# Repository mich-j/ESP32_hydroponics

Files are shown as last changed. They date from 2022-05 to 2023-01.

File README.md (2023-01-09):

# ESP32_hydroponics: IoT hydroponics setup with telemetry

System designed for easy crop cultivation at home, especially herbs and fast-growing small plants like lettuce. Three channels, with continous flow of a nutrient solution, are available, allowing for up to 12 seedlings to be grown at the same time.

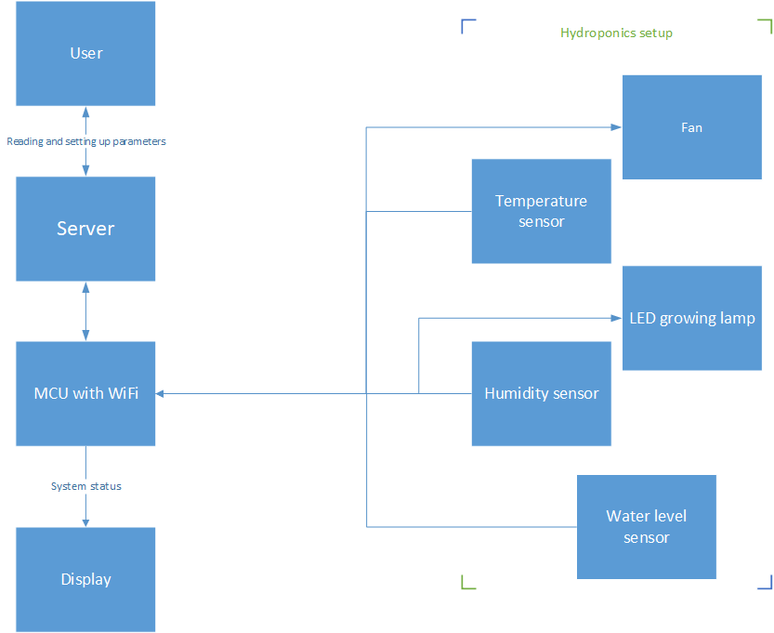
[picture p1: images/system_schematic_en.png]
schematic


ESP32 Devkit module was used to process data from sensors and publish messages with telemetry via MQTT.

Code was written using Arduino Framework for ESP32, in Visual Studio Code with Platformio extension.

### Features
- Air temperature and humidity measurement
- Built as a Nutrient Film Technique (NFT) system
- Remote control via MQTT protocol
- Dashboard with gauges and charts
- PWM LED control
- Low water level alert
- Fan for controlling humidity and supplying oxygen
- OLED screen for easy operation control

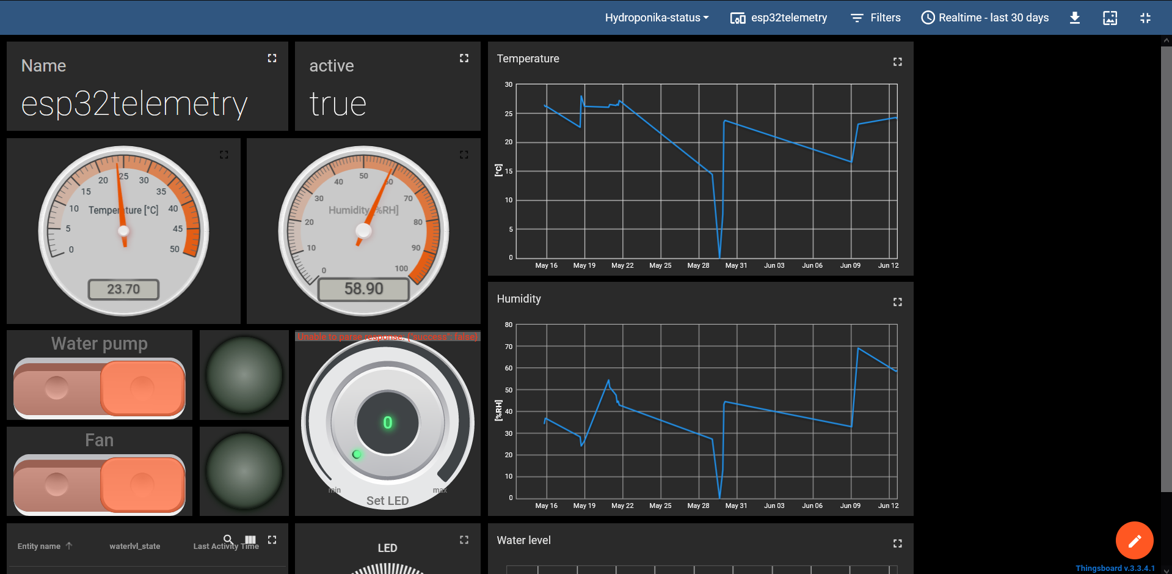
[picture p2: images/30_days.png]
administrator's dashboard

_Dashboard for system's administrator_
  
 ### Communication 

Raspberry Pi 3B+ hosts Thingsboard server, which allows to store sensors' output in a database and display a dashboard with charts and gauges, accessible within local network. User can turn on/off water pump and fan. Moreover, LED intensity can be controlled with a dimmer. Raspberry also works as a MQTT broker and a gateway for communication with Thingsboard.

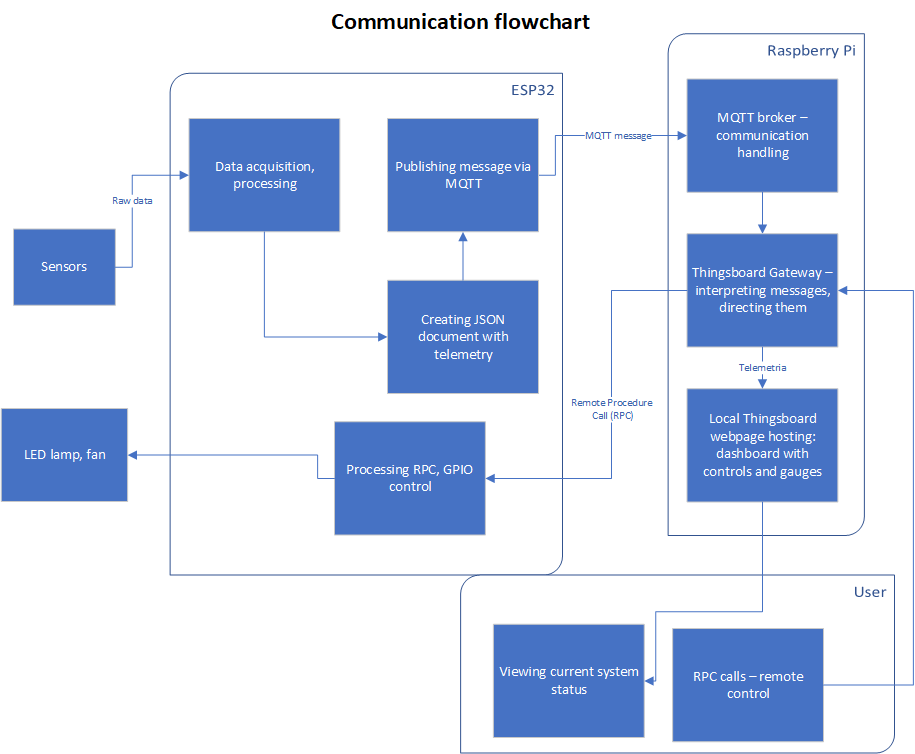
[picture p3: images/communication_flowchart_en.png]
communication schema
 

### Used software:
- [Mosquitto MQTT broker](https://mosquitto.org/)
- [Thingsboard Community server](https://thingsboard.io/)

### Used libraries:
- [SimpleDHT](https://github.com/winlinvip/SimpleDHT) 
- [u8g2](https://github.com/olikraus/u8g2)
- [ESP32 Timer Interrupt](https://github.com/khoih-prog/ESP32TimerInterrupt)
- [PubSub Client](https://github.com/knolleary/pubsubclient)
- [ArduinoJson](https://github.com/bblanchon/ArduinoJson)

### Built prototype

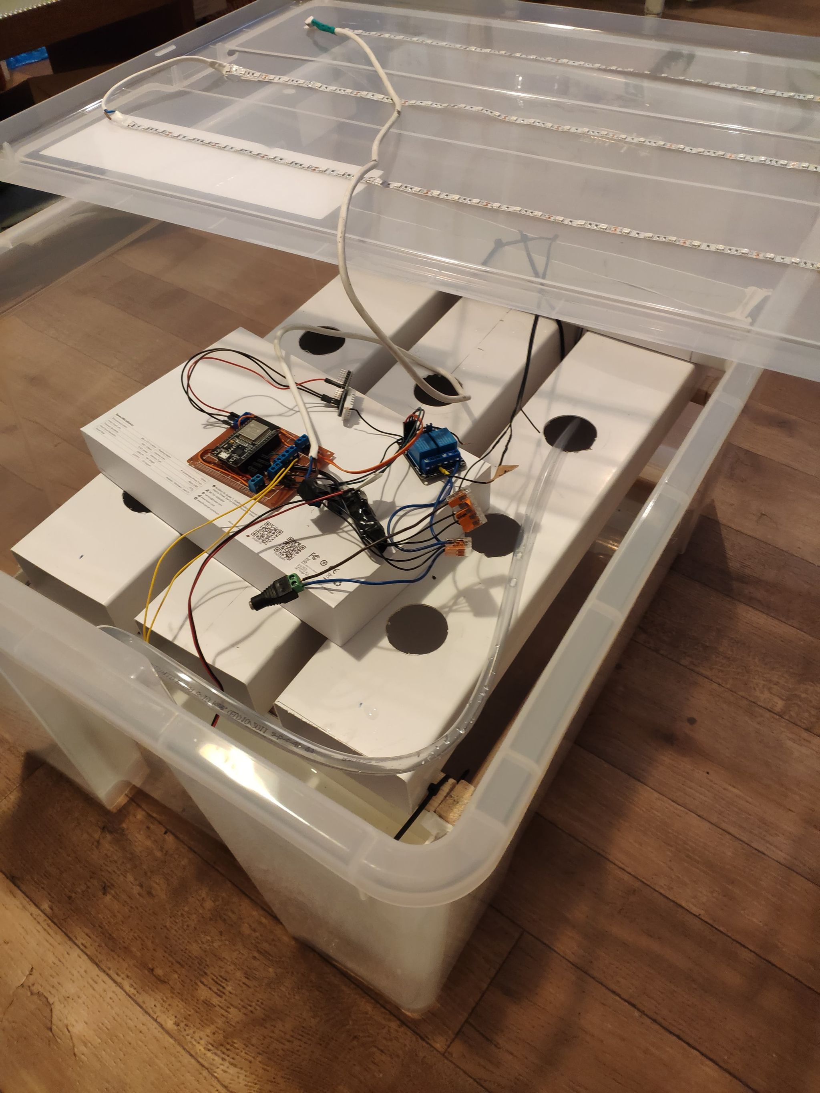
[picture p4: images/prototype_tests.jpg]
Prototype tests


_Prototype during tests_

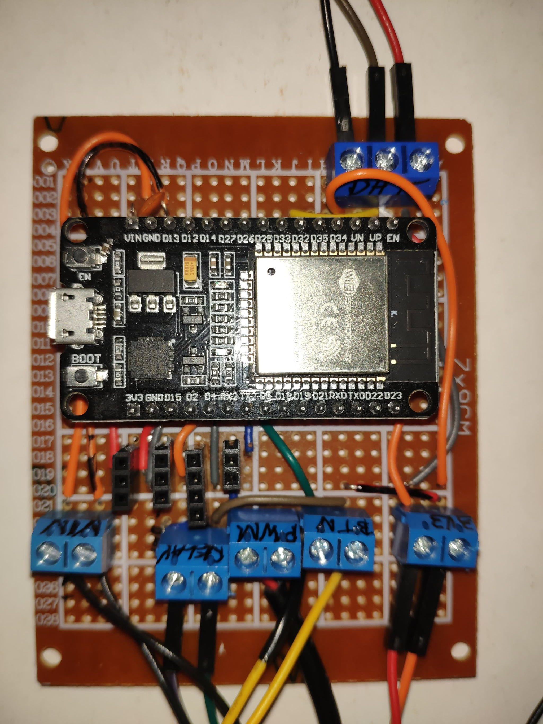
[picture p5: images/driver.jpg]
driver


_Controller based on ESP32_

## More
Documentation (in Polish)

## To-do
- [x] Setting up MQTT broker on RPi 
- [x] Setting up Thingsboard server and Gateway on RPi 
- [x] Sending telemetry to Thingsboard server
- [x] RPC implementation - controlling GPIO and PWM from dashboard
- [x] Building and running actual prototype
- [ ] Finish implementing OLED screen display
- [ ] Add fully autonomous operation mode
- [ ] Improve the construction

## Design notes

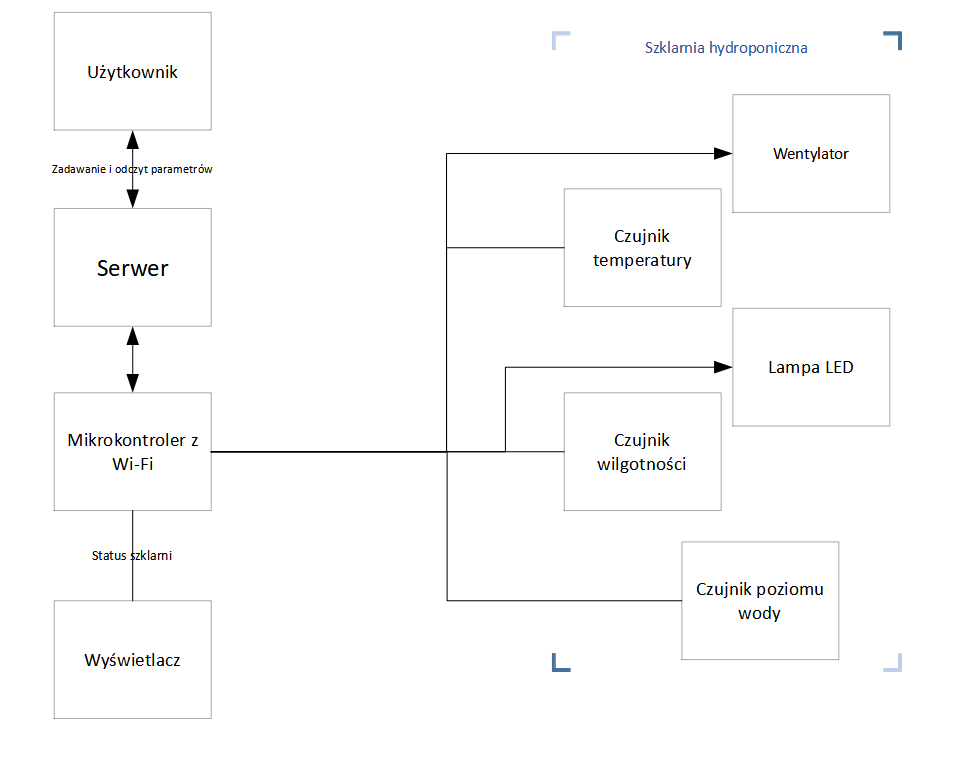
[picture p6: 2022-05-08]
images/system_schematic.png

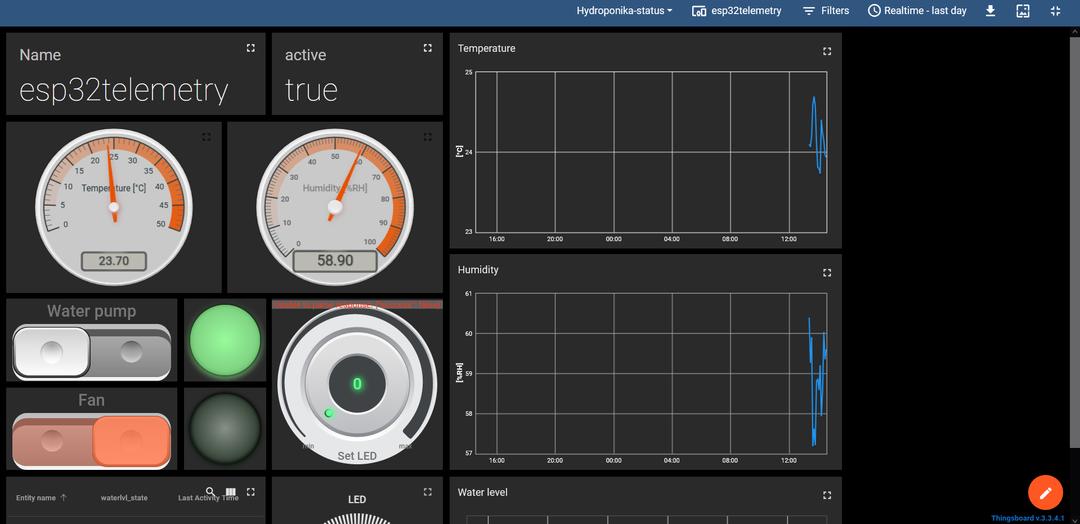
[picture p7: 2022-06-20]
images/last_day.png

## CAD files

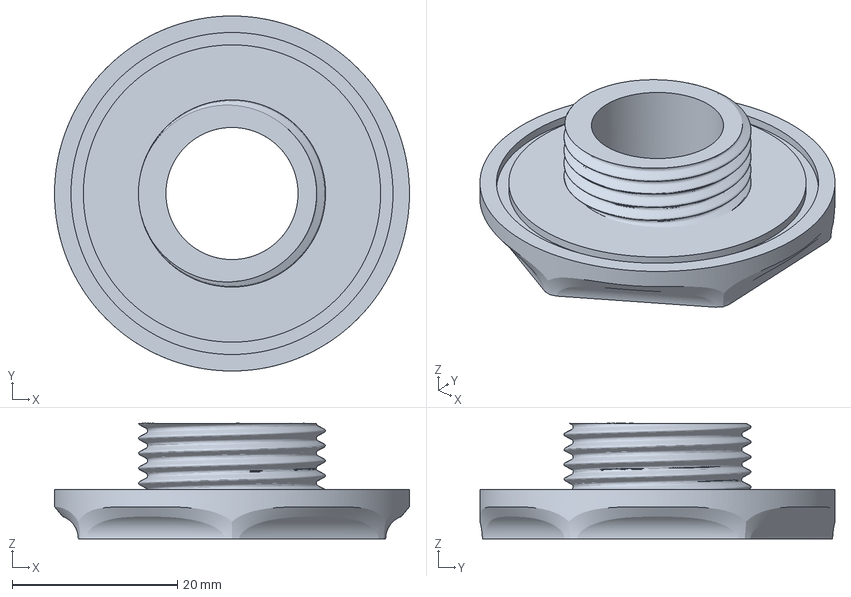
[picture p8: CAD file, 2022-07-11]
construction/przepust_nakretka.3mf
43.0 x 43.0 x 14.0 mm

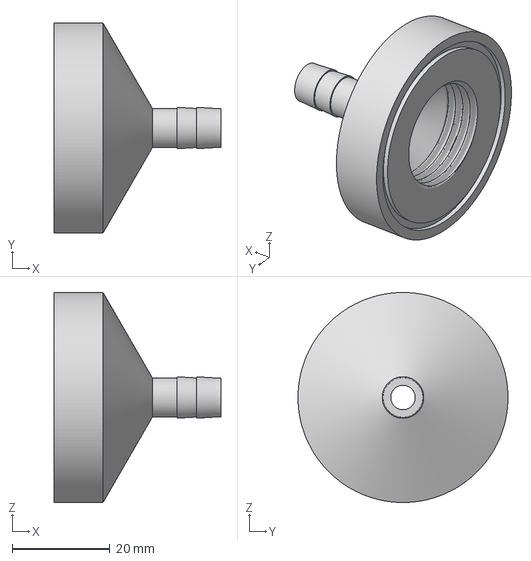
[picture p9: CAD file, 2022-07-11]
construction/przepust_krociec.3mf
34.1 x 43.0 x 43.0 mm

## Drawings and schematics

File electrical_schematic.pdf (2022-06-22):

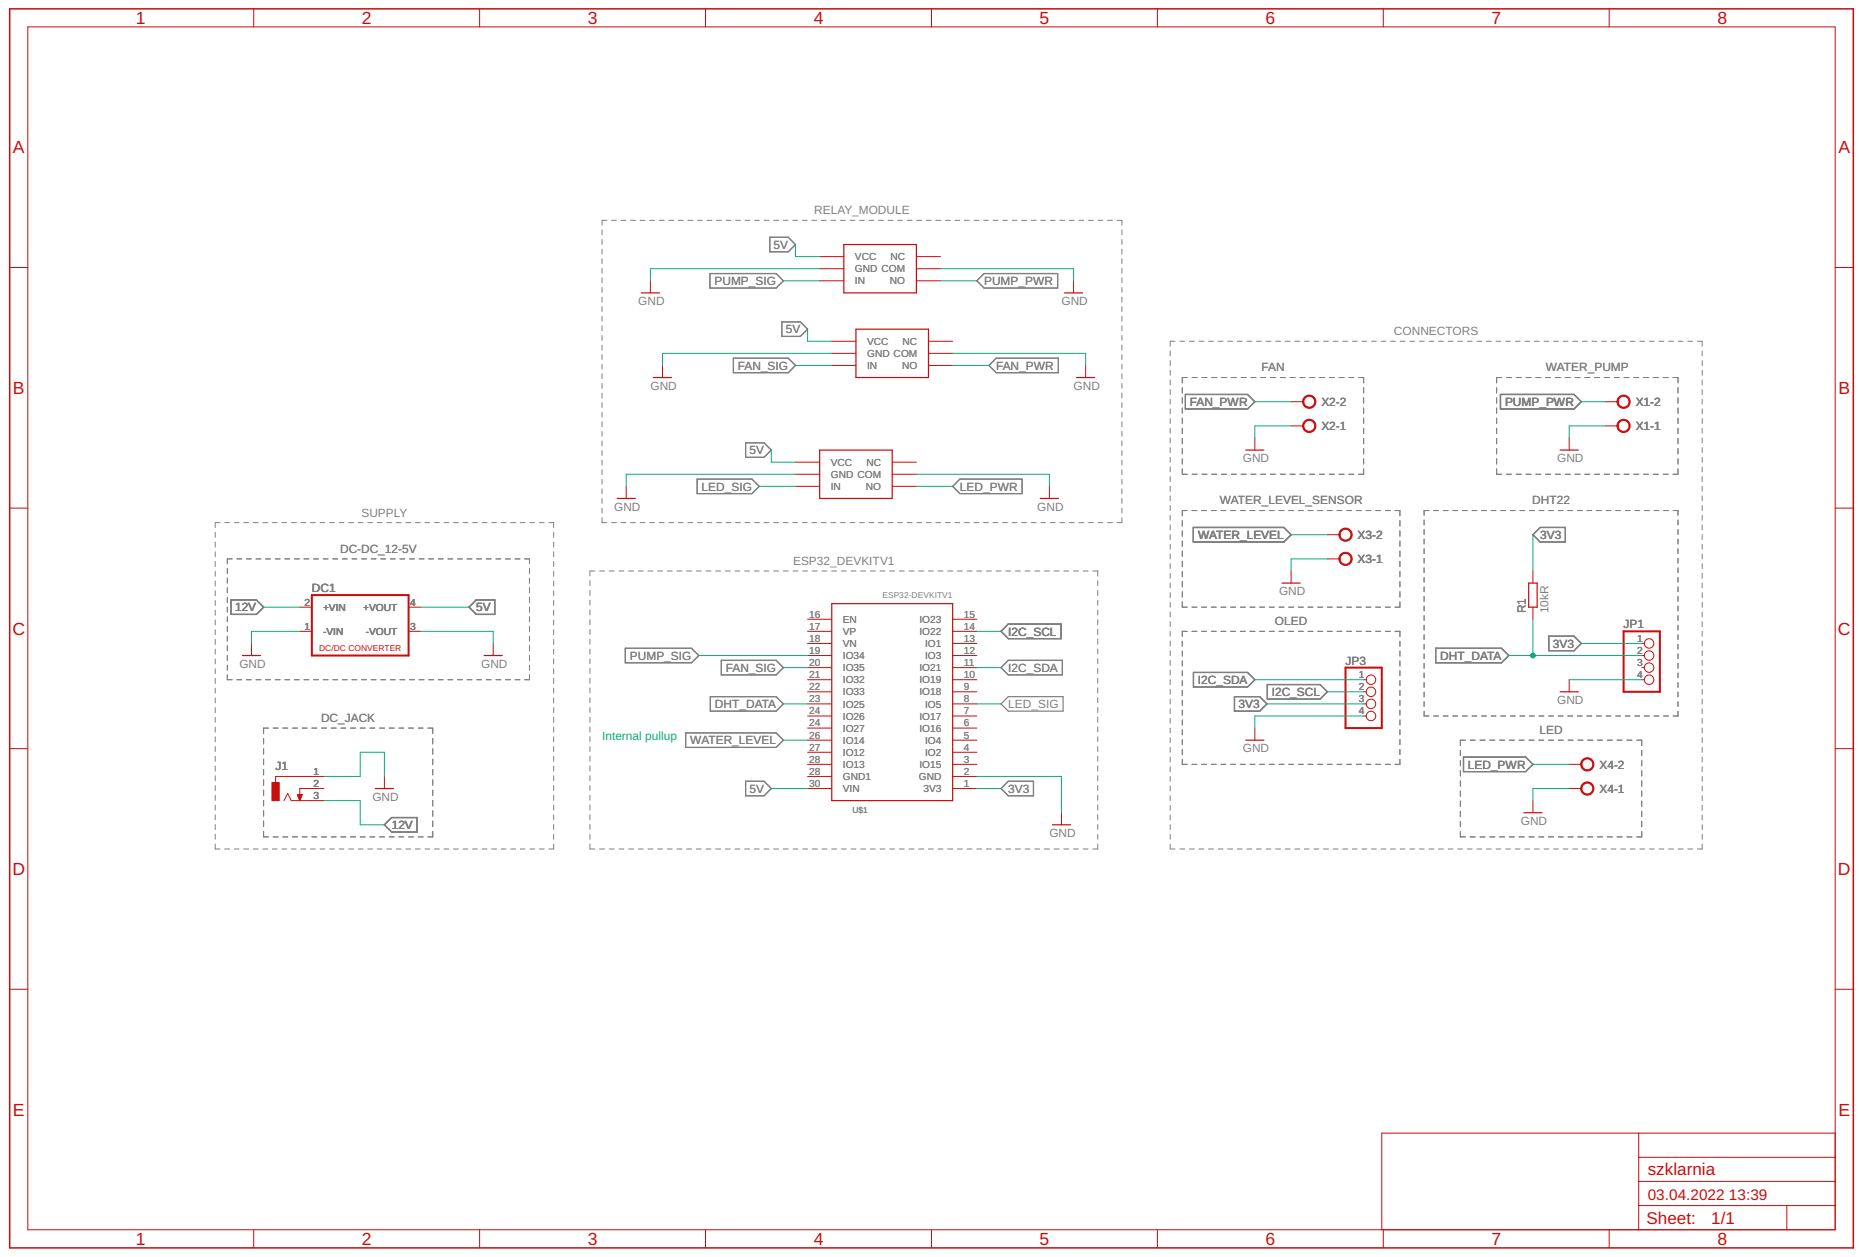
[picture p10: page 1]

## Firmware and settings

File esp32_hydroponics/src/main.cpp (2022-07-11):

/* v2
 * Obecnie działa:
 * > Broker MQTT: Mosquitto na Raspberry Pi
 * > okalny serwer Thingsboard na Raspberry Pi  do wyświetlania wykresów i kontrolek
 * > ESP32 publikuje wiadomości z telemetrią (pomiary z sensorów oraz stan wyjść) w formacie JSON
 * > Program działa w układzie nieblokującym - pomiary i publikacja wywoływana jest przerwaniem timera, w pozostałym czasie wywoływana jest metoda mqtt_client.loop(), co umożliwia nasłuchiwanie żądań ze strony serwera
 * > Możliwe jest wysyłanie żądań RPC (Remote Procedure Call) ze strony serwera, są następnie interpretowane przez klienta (ESP32). W ten sposób możliwe jest zdalne sterowanie pracą systemu
 * > Nie jest wymagana odpowiedź na RPC, ale możliwe jest weryfikowanie poprawności komunikacji przez kontrolki znajdujące się na panelu sterowania. Suwaki on/off służą do wysłania RPC, a stan kontrolek odczytywany jest z telemetrii przesłanej przez klienta.
 * 
 * Uwaga - przekaźniki są rodzaju LOW level trigger - stan niski załącza przekaźnik. Stąd, negacja w funkcji SetRelay()
 * Uwaga2 - pin DATA w DHT22 nie może być podłączony do GPIO oznaczonych jako Input Only xd
 * Repozytorium: https://github.com/mich-j/ESP32_hydroponics
 * 
 * Jan Michalski, 2022
 */

#include <Arduino.h>

#include "ESP32TimerInterrupt.h"
#include <SimpleDHT.h>
#include <U8g2lib.h>
#include <ArduinoJson.h>
#include <PubSubClient.h>
#include "pass.h"
#include <WiFi.h>
#include <string>

#define WATER_OK 1
#define WATER_LOW 0

/// Ustawienia
#define OLED_CLOCK_PIN 22
#define OLED_DATA_PIN 21
#define WATER_PUMP_PIN 4
#define WATER_SENSOR_PIN 5
#define LED_PIN 17 // GPIO17 is TX2 pin
#define LED_CHANNEL 0
#define FAN_PIN 2
#define DHT_PIN 32

#define TEMP_HOT_THRESHOLD 25.0
#define TEMP_COLD_THRESHOLD 20.0

#define TIMER_INTERVAL 120000 // miliseconds // czas pomiędzy kolejnymi przerwaniami timera. Określa, jak często publikowana jest telemetria

uint8_t wifi_status = WL_IDLE_STATUS;
uint8_t lineht;

const char ssid[] = WIFI_SSID;
const char pass[] = WIFI_PASSWORD;
const char mqtt_server[] = MQTT_SERVER;
const uint16_t mqtt_port = MQTT_PORT;
const char device_name[] = "esp32telemetry";
const char data_topic[] = "/sensor/data"; // MQTT topic
const char alarm_topic[] = "alarm";
const char status_topic[] = "status";
const char rpc_request_topic[] = "v1/devices/me/rpc/request/";
const char rpc_response_topic[] = "v1/devices/me/rpc/response/";

static const char * const request_methods[] = {"setValue", "setValueLED"}; // metody używane jako żądania RPC - jednocześnie nazwy tematów
const uint8_t request_methods_qty = 2;
// const char * request_method1 = "setValue";
// const char * request_method2 = "setValueLED";


volatile bool tim_flg = false;
void callback(char *topic, byte *payload, unsigned int length);

float_t temperature = 0;
float_t humidity = 0;
uint8_t water_level = 0;
uint8_t water_pump = 0;
uint8_t led_pwm = 0;
uint8_t fan_state = 0;

// konstruktory
SimpleDHT22 dht22(DHT_PIN);
U8G2_SSD1306_128X32_UNIVISION_F_SW_I2C u8g2(U8G2_R0, OLED_CLOCK_PIN, OLED_DATA_PIN, /* reset=*/U8X8_PIN_NONE);

WiFiClient esp32wifi;
PubSubClient mqtt_client(esp32wifi);

ESP32Timer ITImer0(0);

// Function declarations
void SetRelay(const char *comp, uint8_t state)
{
  uint8_t pin = 0;

  if (strcmp(comp, "fan") == 0)
  {
    pin = FAN_PIN;
    fan_state = state;
   
  }
  if (strcmp(comp, "water_pump") == 0)
  {
    pin = WATER_PUMP_PIN;
    water_pump = state;
  
  }

  digitalWrite(pin, !state);
}

void setPWM(uint8_t channel, uint8_t dutyCycle)
{
  ledcWrite(channel, dutyCycle);
}

void GetWaterLevel(uint8_t *pstate)
{
  *pstate = digitalRead(WATER_SENSOR_PIN);
}

void updateAttributes()
{
  char mqtt_msg[255];
  StaticJsonDocument<255> doc;
  doc["serialNumber"] = device_name;
  doc["sensorType"] = "Hydroponics";
  doc["sensorModel"] = "telemetry";
  doc["temp"] = temperature;
  doc["hum"] = humidity;
  doc["waterlvl"] = water_level;
  doc["led_pwm"] = led_pwm;
  doc["fan_state"] = fan_state;
  doc["water_pump_state"] = water_pump;

  //petla
  doc[getnazwa[i]] = getvalue[i];

  serializeJson(doc, mqtt_msg);
  mqtt_client.publish(data_topic, mqtt_msg);
  Serial.println("Publishing attributes");
}

void callback(char *topic, byte *payload, unsigned int length)
{
  // Funkcja wywoływana w momencie odebrania wiadomości w subskrybowanym temacie
  // Serwer publikuje tam kolejne tematy, każdy ma inną nazwę - jest to ID żądania RPC
  // Odpowiedź klienta jest publikowana w temacie o takiej samej nazwie, jak żądanie. Dzięki temu możliwe jest potwierdzanie odczytu wiadomości.

  /* Odczytanie nazwy tematu, który stanowi jego unikalny numer. Działa pod warunkiem, że ilość podtematów, począwszy od v1, jest stała xD */
  // strtok działa tak, że pierwszy znak określony w argumencie, zastępuje NULL. Zwraca wskaźnik na początek łańcucha znaków, od którego zaczęło się poszukiwanie. Jeśli chcemy szukać dalej, wywołujemy ją z argumentem NULL.
  char *request_id;
  char *ptr;
  char *methodName;
  ptr = strtok(topic, "/");

  uint8_t cnt = 0;
  while (ptr != NULL)
  {
    ptr = strtok(NULL, "/");
    cnt++;

    if (cnt == 5) // w piątym+1 segmencie oddzielonym znakiem / znajduje się nazwa metody (wycięta z nazwy tematu)
    {
      methodName = ptr;
    }

    if (cnt >= 6)
    {
      request_id = ptr; // analogicznie, kolejny segment zawiera identyfikator żądania
      ptr = NULL;
    }
  }

  /* odczytanie i obsługa treści wiadomości */

  if (strcmp(methodName, "setValueLED") == 0)
  {
    payload[length] = '\0'; // przekształcenie w ciąg znaków poprzez doklejenie NULL z prawej strony
    led_pwm = atoi((char *)payload);
    Serial.printf("LED PWM: %d \n", led_pwm);
    setPWM(LED_CHANNEL, led_pwm);
  }
  else if (strcmp(methodName, "setValue") == 0)
  {
    StaticJsonDocument<1000> doc;
    deserializeJson(doc, payload);
    char const *component = doc["component"];
    uint8_t state = doc["enabled"];
    Serial.printf("Set %s in state %d \n", component, state);
    SetRelay(component, state);
    serializeJsonPretty(doc, Serial);
    Serial.print("\n");
    doc.clear();
  }
  else{
    Serial.println("Nieznane zadanie RPC");
  }

  updateAttributes();
}

void oledPrint(uint8_t cur_x, uint8_t cur_y, char *buffer)
{
  u8g2.setCursor(cur_x, cur_y);
  u8g2.print(buffer);
  u8g2.sendBuffer();

  Serial.println(buffer); // buffer to char z nazwą tematu w którym zostanie opublikowana odpowiedź
}

void setupWIFI(void)
{

  WiFi.mode(WIFI_STA);
  mqtt_client.setServer(mqtt_server, mqtt_port);
  oledPrint(0, 10, "connecting");

  uint8_t cnt = 0;
  while (WiFi.status() != WL_CONNECTED)
  {
    WiFi.hostname("ESP-host");
    WiFi.begin(ssid, pass);
    WiFi.setSleep(false);
    oledPrint(cnt * 5, lineht, ".");

    delay(5000);
    cnt++;
  }
  u8g2.clear();
  Serial.print("Polaczono z siecia ");
  Serial.println(WiFi.SSID());
  Serial.print("Adres IP: ");
  Serial.println(WiFi.localIP());
}

void setupMQTT(void)
{
  const char *client_id = CLIENT_ID;
  const char *client_username = CLIENT_USERNAME;
  const char *client_pass = CLIENT_PASS;

  char msg[255];
  StaticJsonDocument<255> doc;

  while (!mqtt_client.connected())
  {
    mqtt_client.connect(client_id, client_username, client_pass);
    Serial.println("connecting to broker: ");
    Serial.println(mqtt_client.state());

    delay(5000);
  }

  // opublikowanie w odpowiednim temacie informacji o sukcesie połączenia.
  
  doc["serialNumber"] = device_name;
  serializeJson(doc, msg);
  mqtt_client.publish("/sensor/connect", msg);
 
  for (uint8_t i = 0; i < request_methods_qty; i++)
  {
    char topic[40];
    strcpy(topic, rpc_request_topic);
    strcat(topic, request_methods[i]);
    strcat(topic, "/+");
    mqtt_client.subscribe(topic);
  }
  
  // mqtt_client.subscribe("v1/devices/me/rpc/request/setValueLED/+");
  mqtt_client.setCallback(callback);
}

bool IRAM_ATTR TimerHandler(void *timerNumber)
{
  tim_flg = true;

  return true;
}

void setup()
{
  u8g2.begin();
  u8g2.setFont(u8g2_font_ncenB08_tr);
  u8g2.clear();
  lineht = u8g2.getMaxCharHeight() + 10;

  Serial.begin(9600);
  Serial.println("Uruchamianie szklarni");
  Serial.printf("CPU speed: %d MHz\n", getCpuFrequencyMhz());

  setupWIFI();
  setupMQTT();

  // setup pinów
  ledcSetup(LED_CHANNEL, 1000, 8);
  ledcAttachPin(LED_PIN, LED_CHANNEL);
  pinMode(WATER_SENSOR_PIN, INPUT_PULLUP);
  pinMode(FAN_PIN, OUTPUT);
  pinMode(WATER_PUMP_PIN, OUTPUT);
  digitalWrite(FAN_PIN, HIGH);
  digitalWrite(WATER_PUMP_PIN, HIGH);

  delay(5000);

  // setup timera
  if (ITImer0.attachInterruptInterval(TIMER_INTERVAL * 1000, TimerHandler))
  {
    Serial.println("Konfiguracja timera poprawna :)");
  }
  else
  {
    Serial.println("timer nie dziala :C");
  }
}

void loop()
{
  if (tim_flg == true)
  {
    if (WiFi.status() != WL_CONNECTED || mqtt_client.connected() != true)
    {
      // jeśli brak połączenia z WiFi, lub utracono połączenie z brokerem, próbuj ponownie
      setupWIFI();
      setupMQTT();
    }

    if (true){
      char *buf = new char[255];

      if (int DHTerror = dht22.read2(&temperature, &humidity, NULL) != SimpleDHTErrSuccess)
      {
        u8g2.setCursor(0, 10);
        u8g2.print(SimpleDHTErrCode(DHTerror));
        u8g2.sendBuffer();
      }

      u8g2.clear();
      sprintf(buf, "Temp: %.1f *C", temperature);
      oledPrint(0, 10, buf);
      sprintf(buf, "Hum: %d RH", (int)humidity);
      oledPrint(0, 10 + lineht, buf);

      StaticJsonDocument<255> doc;
      StaticJsonDocument<255> alrm;

      if (temperature > TEMP_HOT_THRESHOLD)
      {
        alrm["temp_alrm"] = "HOT";
      }
      else if (temperature < TEMP_COLD_THRESHOLD)
      {
        alrm["temp_alrm"] = "COLD";
      }

      else
      {
        alrm["temp_alrm"] = "OK";
      }

      // formatowanie dokumentu JSON z telemetrią do publikacji
      updateAttributes();

      doc.clear();

      GetWaterLevel(&water_level);
      Serial.printf("Poziom wody : %d \n", water_level);
    }

  
    tim_flg = false;
  } // koniec zadania uruchamianego poprzez timer

  mqtt_client.loop();
}

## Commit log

2022-04-18 established connection with mqtt broker
    [main.cpp]
2022-05-08 Timer interrupts working
2022-06-22 uploaded few schematics
